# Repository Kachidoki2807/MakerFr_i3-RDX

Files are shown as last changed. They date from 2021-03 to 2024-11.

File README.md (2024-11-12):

# MakerFr i3-RDX <!-- omit in toc -->

Ce dépôt contient tout le nécessaire pour construire une MakerFr i3-RDX.
<p align="center">
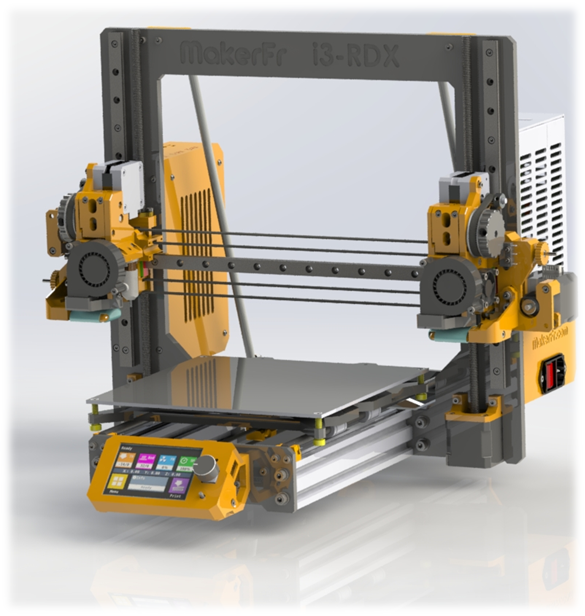
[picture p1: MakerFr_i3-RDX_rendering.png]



</p>

# Table des contenus <!-- omit in toc -->
- [Tutoriel de montage](#tutoriel-de-montage)
- [Cadre](#cadre)
- [Pièces à imprimer](#pièces-à-imprimer)
- [Pièces à sourcer](#pièces-à-sourcer)
- [Firmware BTT Octopus v1.1](#firmware-btt-skr-pro-12)
- [Firmware BTT TFT35](#firmware-btt-tft35)
- [PrusaSlicer - MakerFr Edition + .INI pour PrusaSlicer "normal"](#prusaslicer---makerfr-edition)

## Tutoriel de montage
[Disponible dans le dépôt](./PDF/)

## Cadre

[Disponible dans le dépôt](./Frame/)

## Pièces à imprimer

[Disponibles dans le dépôt](./STL/)

## Pièces à sourcer

[Disponibles dans le dépôt](./BOM/)

## Firmware BTT Octopus 1.1 (version 2.1.2.4 upgradé)

### Pourquoi cette version spéciale ? <!-- omit in toc -->
Dans la release 2.0.7.2 de MarlinFirmware, il y a un bug concernant la ventilation, empêchant l'utilisation correcte des modes de duplication (Duplication / Miroir). Ce bug a été corrigé par l'équipe de MakerFr et intégré dans MarlinFirmware, cependant il n'y a pas eu de nouvelle release depuis la correction. Afin de garantir la cohérence du code et de sa configuration (la branche bugfix est en constante évolution et n'est pas garantie fonctionnelle à tout instant), il est nécessaire de proposer une version spécifique MakerFr dans un état stable.

Il s'agit d'une branche basée sur le tag 2.0.7.2 dans laquelle ont été intégrés la configuration pour la MakerFr i3-RDX ainsi qu'un cherry pick (sorte de copier/coller) du correctif qui a été introduit dans la branche bugfix.

~~Ceci en attendant une éventuelle 2.0.7.3 qui intègrera nativement ce correctif.~~ Version 2.1.2.4 disponible

### Fichiers <!-- omit in toc -->
[Sources de MarlinFirmware modifié](https://github.com/Kachidoki2807/Marlin/tree/MakerFr_2.0.7.2_bugfix%2321206)

[Binaire pré-compilé pour Octopus 1.1 de BTT](/Firmware/BTT_Octopus/firmware.bin)

Le fichier .bin est à mettre sur la carte µSD de la BTT SKR PRO 1.2. Il sera automatiquement renommé en .CUR après la mise à jour.

## Firmware BTT TFT35
Concernant le TFT, le problème est tout autre. Il n'y a aucune gestion de version dans le dépôt officiel du constructeur. Ainsi le firmware évolue de jour en jour, sans aucune cohérence ni garantie d'un état stable. La maintenance devient alors très pénible.

~~Pour palier à cela, chez MakerFr on vous propose une "version" figée qui date de début 2021, avec laquelle nous avons travaillé depuis. La configuration est adaptée à l'i3-RDX.~~ MISE A JOUR FAITE EN 2024.

[Binaire pré-compilé pour le TFT35 de BTT](Firmware/BTT_TFT35/BIGTREE_TFT35_V3.0.26.x.bin)

Copier tout le contenu de ce dossier sur la carte SD du BTT TFT35. Les différents éléments seront automatiquement renommés en .CUR après la mise à jour.

> **Astuce :** N'oubliez pas qu'il vous est possible de télécharger le contenu de tout ce présent dépôt d'un seul bloc en [ZIP](../../archive/refs/heads/master.zip).

## PrusaSlicer - MakerFr Edition (Fichiers .ini pour PrusaSlicer "normal" dispo)

### Pourquoi cette édition ? <!-- omit in toc -->
Cette édition spéciale corrige certaines imperfections de PrusaSlicer concernant la gestion de la ventilation, ainsi que la dimension de la tour de purge.

Mais elle intègre également un tout nouveau profil constructeur, qui contient une série de paramètres prédéfinis. Ainsi il n'y a qu'à passer par le configurateur pour avoir un slicer en état de générer un G-Code compatible avec l'i3-RDX d'un clic.

Une réflexion est en cours sur la suite à donner à cette édition, des tickets supports on été ouvert chez Prusa, mais pas encore résolu. Concernant le profil constructeur, il pourra également évoluer indépendamment du slicer. Une intégration dans la base de profils de Prusa est envisageable, mais il faudra probablement l'étoffer un peu avant d'en arriver là.

### Fichiers <!-- omit in toc -->
Les sources seront peut-être mises à disposition dans l'avenir.

[Application pré-compilée pour Windows](../../raw/master/Slicer/PrusaSlicer%20-%20MakerFr%20Edition.zip)

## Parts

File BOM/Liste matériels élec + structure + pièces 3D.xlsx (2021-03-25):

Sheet: visserie
Tete / Type | Designation | Elec unit | EX1 | EX2 | Structure | Spool holder x 2 | Nb unités dénombré | arrondi sup | vis express | lot de | Tarif lot | Nb lot | PU ( pour info)
FHC | M3x8 | 0 | 0 | 0 | 2 | 0 | 2 | 5 | https://www.vis-express.fr/fr/vis-mx-fhc-inox-a4-din-7991/38157-936385-vis-metaux-fhc-tete-fraisee-empreinte-hexagonale-creuse-3x6-inox-a4-3663072419063.html | 10 | 0.23 | 1 | 0.02
FHC | M3x12 | 0 | 0 | 0 | 2 | 0 | 2 | 5
FHC | M3x25 | 0 | 0 | 0 | 4 | 0 | 4 | 10
CHC | M2x10 | 0 | 2 | 2 | 6 | 0 | 10 | 10
CHC | M3x6 | 0 | 3 | 1 | 18 | 0 | 22 | 30 | https://www.vis-express.fr/fr/vmx-chc-t-basse-a2-din-7984/40584-464799-vis-metaux-chc-btr-tete-bas-hc2-3x6-filetage-total-inox-a2-3663072196216.html | 10 | 3.6 | 1 | 0.12
CHC | M3x8 | 2 | 3 | 2 | 24 | 0 | 31 | 40 | https://www.vis-express.fr/fr/vmx-chc-t-basse-a2-din-7984/40585-970488-vis-metaux-chc-btr-tete-bas-hc2-3x8-filetage-total-inox-a2-3663072218895.html | 10 | 3.6 | 1 | 0.12
CHC | M3x10 | 0 | 0 | 0 | 12 | 0 | 12 | 30 | https://www.vis-express.fr/fr/vmx-chc-t-basse-a2-din-7984/40586-464815-vis-metaux-chc-btr-tete-bas-hc2-3x10-filetage-total-inox-a2-3663072196223.html | 10 | 0.23 | 3 | 0.02
CHC | M3x12 | 4 | 0 | 0 | 18 | 8 | 30 | 30
CHC | M3x16 | 2 | 4 | 4 | 38 | 2 | 50 | 50 | https://www.vis-express.fr/fr/vmx-chc-t-basse-a2-din-7984/40588-464831-vis-metaux-chc-btr-tete-bas-hc2-3x16-filetee-sur-12-inox-a2-3663072196230.html | 30 | 3.76 | 2 | 0.12
 |  |  |  |  |  | 0 | 0 |  |  | 10 | 2.76 | 1 | 0.28
CHC | M3x20 | 0 | 4 | 4 | 15 | 0 | 23 | 30 | https://www.vis-express.fr/fr/vmx-chc-t-basse-a2-din-7984/40589-464839-vis-metaux-chc-btr-tete-bas-hc2-3x20-filetee-sur-12-inox-a2-3663072223165.html | 10 | 0.24 | 1 | 0.02
CHC | M3x30 | 0 | 4 | 4 | 2 | 0 | 10 | 10 | https://www.vis-express.fr/fr/vmx-chc-t-basse-a2-din-7984/40591-464855-vis-metaux-chc-btr-tete-bas-hc2-3x30-filetee-sur-12-inox-a2-3663072378766.html | 10 | 0.54 | 2 | 0.05
CHC | M4x6 | 0 | 0 | 0 | 5 | 0 | 5 | 5
CHC | M4x8 | 0 | 0 | 0 | 0 | 0 | 0 | 5
CHC | M4x16 | 4 | 0 | 0 | 0 | 0 | 4 | 5
CHC | M5x16 | 0 | 0 | 0 | 16 | 0 | 16 | 20 | https://www.vis-express.fr/fr/vis-metaux-chc-btr-trou-de-guidage-acier/31608-980083-vis-metaux-chc-btr-5x16-classe-88-tete-basse-trou-acier-3663072368194.html | 20 | 3.18 | 2 | 0.32
H | M5x30 | 0 | 0 | 1 | 0 | 0 | 1 | 1
 | Ecrou M5 | 0 | 0 | 1 | 0 | 0 | 1 | 1
 | Ecrou M4 | 4 | 0 | 0 | 0 | 0 | 4 | 5
 | Ecrou M3 0.8d | 0 | 10 | 10 | 81 | 10 | 111 | 120
 | Ecrou M8 | 0 | 0 | 0 | 6 | 0 | 6 | 10
Plate étroite | Rondelle 3 |  |  |  |  |  | 32 | 50
Plate étroite | Rondelle 5 | 6 | 0 | 3 | 16 | 0 | 25 | 30
Plate étroite | Rondelle 8 | 0 | 0 | 0 | 4 | 0 | 4 | 5
 | ressort L12 mm D 5 interne | 0 | 0 | 1 | 0 | 0 | 1 | 1 | issu de la liste matos general, ressort d'UM2

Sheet: matos general
check | désignation | Source | Prix Unitaire | Nb | Ss total
Mécanique
o | Vslot noir 400 mm ( pour recoupe de 2 x ( 235mm + 105mm) ) | https://www.aliexpress.com/item/Black-100-500mm-2040-V-Slot-Aluminum-for-CNC-DIY-Laser-Engraving-3D-Printers-Camera-Slider/4001287484543.html | 7.34 € | 2 | 14.68 €
o | MGN12 H + rail 400mm | https://fr.aliexpress.com/item/32861278496.html?spm=a2g0s.9042311.0.0.27426c37sMZzYj | 13.95 € | 1 | 13.95 €
o | MGN12 H + rail 300mm | https://www.aliexpress.com/item/12mm-Linear-Guide-MGN12-L-100-200-300-350-400-450-500-550-600-700-800/32861278496.html | 12.12 € | 2 | 24.24 €
o | chariot MGN12H | https://fr.aliexpress.com/item/32861278496.html?spm=a2g0s.9042311.0.0.27426c37sMZzYj | 5.16 € | 1 | 5.16 €
o | Pignon GT2 16 dents alesage 5 mm | https://www.aliexpress.com/item/5PCS-16-teeth-GT2-Timing-Pulley-Bore-5mm-for-Rubber-2GT-Open-Timing-belt-width-6mm/33017482340.html | 2.83 € | 1 | 2.83 €
o | Poulie GT2 16 dents sur roulements - axe 3 mm | https://www.aliexpress.com/item/16T-20T-GT2-Aluminum-Timing-Pulley-With-Without-Tooth-For-DIY-3D-Printer/32885958954.html | 0.64 € | 3 | 1.92 €
o | Pignon GT2 60 dents axe 5 mm - lot de 3 | https://www.aliexpress.com/item/60-Teeth-GT2-Timing-Pulley-Bore-5-6-6-35-8-10-12-14-15mm-for/32993060755.html | 10.87 € | 1 | 10.87 €
o | Courroie ouverte 2GT par 5m, choisir "Type C" | https://www.aliexpress.com/item/5M-2GT-open-timing-Belt-6mm-PU-with-Steel-Core-Rubber-fiberglass-timing-belt-GT2-6mm/32859410237.html | 3.45 € | 1 | 3.45 €
o | Courroie fermée 2GT L=150 mm | https://www.aliexpress.com/item/GKTOOLS-C-3-3D-Printer-Parts-GT2-6mm-Closed-Loop-Rubber-Timing-Belt-2GT-Length-140/4000307058782.html | 0.34 € | 2 | 0.68 €
o | Lot 4 guidages linéaires à billes LM8UU | https://www.aliexpress.com/item/4PCS-LM8UU-Linear-Bearings-LM3UU-LM4UU-LM5UU-LM6UU-LM10UU-LM12UU-LM13UU-LM16UU-LM20UU-Linear-Bushing-8mm/32873055960.html | 3.00 € | 1 | 3.00 €
o | Tige lisse D=8 mm L=400 mm | https://www.aliexpress.com/item/6mm-8mm-10mm-12mm-16mm-linear-shaft-L-100-150-200-250-300-350-400-500/32560455225.html | 7.85 € | 2 | 15.70 €
o | Lot de 20 spacers 8 mm M3 | https://www.aliexpress.com/item/5-50pcs-Hex-Female-to-Female-M2-M2-5-M3-M4-M5-brass-standoff-spacer-Hexagonal/4000239735518.html | 0.94 € | 1 | 0.94 €
o | Kit bondtech gears | https://www.aliexpress.com/item/Drivegear-kit-dual-drive-gear-extruder-kit-Cloned-Btech-upgrade-for-extruder-for-Prusa-i3-3d/32959764680.html | 6.74 € | 2 | 13.48 €
o | Feuille auto collante bed | https://www.aliexpress.com/item/3D-printer-Parts-1-pcs-Frosted-Heated-bed-Sticker-printing-Build-Sheets-build-plate-tape-Platform/32842476025.html | 3.27 € | 2 | 6.54 €
 | 2 Pads silicone prédécoupés |  | 0.00 € | 1 | 0.00 €
 | Cadre spécifique i3 RDX - valchromat |  | 0.00 € | 1 | 0.00 €
 | Kit de pieces imprimées i3 RDX |  | 0.00 € | 1 | 0.00 €
o | kit 5 ressort UM2 | https://fr.aliexpress.com/item/32604418352.html?scm_id=1007.14976.191224.0&scm-url=1007.14976.191224.0 | 0.71 € | 1 | 0.71 €
 | Tige lisse 5mm longueur 51mm | Casto, Leroy merlin |  | 1 | 0.00 €
 | Tige fileté de diamètre 8mm L = 360mm | Casto, Leroy merlin |  | 1 | 0.00 €
 | 4 Roulement MR105RS | https://fr.aliexpress.com/item/32949998854.html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 | 6.94 | 1 | 6.94 €
o | Lot de 4 vis ajustement bed + ressort 15x6x3, couleur au choix | https://fr.aliexpress.com/item/4000143856235.html | 2.73 | 1 | 2.73 €
 |  |  |  | Sous-total | 127.82 €
Electricité
 | Machine bien bruyante !!!!! ;-) |  |  |  |  |  | Option SILENCE = "fan 40 mm sliencieux" pour hotends
 |  |  |  |  |  |  |  |  | Prix unitaire | Nb | Ss total
o | Heat bed aimanté + feuille acier | https://www.aliexpress.com/item/220-220mm-3D-Printer-MK3-Magnetic-Heated-Bed-24V-Wiring-Thermistor-Kit-With-Steel-Sheet-For/32960562213.html | 35.20 € | 1 | 35.20 €
o | Alim 24 V 400 W | https://www.aliexpress.com/item/Switch-Power-Supply-for-Led-strip-Adapter-AC-110-220V-to-DC-24V-20A-480W-Transformer/32771311343.html | 19.17 € | 1 | 19.17 € |  | Fan 4010 de prusa mk3, lot de 2 (sur Store Fysetc sur le web) | https://www.fysetc.com/products/fysetc-prusa-i3-mk3-cool-blower-fan-4010-40x40x10mm-dc-5v-0-2a-hotend-cooler-radiator-for-3d-printer-diy-parts-accessories-2pc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 | 12.99 | 1 | 12.99
o | BTT SKR Pro 1.2 + 6 TMC2209 | https://fr.aliexpress.com/item/33037993926.html?spm=a2g0w.12010612.8148356.31.29f41e73Z66uXW | 63.74 € | 1 | 63.74 € |  | OU
o | BL Touch Original + rallonge fils | https://fr.aliexpress.com/item/33025648093.html?spm=a2g0w.12010612.8148356.1.6fb7d78azxapbg | 29.83 € | 1 | 29.83 € |  | régulateur DC/DC 24V / ajustable | https://www.amazon.fr/VABNEER-LM2596S-Alimentation-convertisseur-Converter/dp/B072MQYJ93/ | 3.33 € | 1 | 3.33 €
o | E3D v6 clone kit (hotend,etc dont fan 30 mm) - 24 V- 1.75 mm All metal | https://fr.aliexpress.com/item/32844028127.html | 13.79 € | 2 | 27.58 € | si pas fan 30mm | Fan noctua 5V | https://www.amazon.fr/Noctua-NF-A4x10-FLX-Ventilateur-40x40x10mm/dp/B00NEMGCIA?th=1 | 12.90 € | 2 | 25.80 €
o | Ecran TFT35 V3.0 Bigtreetech | https://fr.aliexpress.com/item/4000051197496.html | 23.35 € | 1 | 23.35 €
o | Blower 5015 | https://www.aliexpress.com/item/Aokin-DC-12V-24V-50mm-Blow-Radial-Cooling-Fan-Hotend-Extruder-For-RepRap-3D-Printer-Accessories/32972702280.html | 1.49 € | 2 | 2.98 € | OU | 2 Blower 5 V FYSETC prusa i3 Mk3 | https://fr.aliexpress.com/item/32961572014.html | 5.4 | 1 | 5.4
o | Lot 10 mico switches sans levier | https://www.aliexpress.com/item/10-PCS-LOT-Limit-Switch-3-Pin-2-Pin-High-quality-and-long-life-All-New/32273125391.html | 1.36 € | 1 | 1.36 € |  | (ou sur Store Fysetc sur le web) | https://www.fysetc.com/products/prusa-i3-mk3-3d-printer-parts-dc-5v-5015-50mm-blow-radial-cooling-fan-hydraulic-sleeve-bearing-front-print-fan-cooler-radiator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 | 2.9 | 2 | 5.8
o | Gaine tressée 4 mm | https://www.aliexpress.com/item/5-10M-Black-Insulated-Braid-Sleeving-2-4-6-8-10-12-15-20-25mm-Tight/4000111680202.html | 2.11 € | 1 | 2.11 €
o | Gaine tressée 10 mm | https://www.aliexpress.com/item/5-10M-Black-Insulated-Braid-Sleeving-2-4-6-8-10-12-15-20-25mm-Tight/4000111680202.html | 3.37 € | 1 | 3.37 €
o | Fils N+R 16AWG 1m + 1m | https://www.aliexpress.com/item/1meter-Black-1meter-Red-Silicon-Wire-12AWG-14AWG-16AWG-22AWG-24AWG-Heatproof-Soft-Silicone-Silica-Gel/32807592656.html | 3.11 € | 2 | 6.22 €
o | Cable N+R 18AWG 5m | https://fr.aliexpress.com/item/32867632555.html | 4.19 € | 1 | 4.19 € |  | ceci est une variante de contitution stepper Z en 3 pîeces.
o | Lot 3 steppers nema 17 42 | https://www.aliexpress.com/item/Rtelligent-Nema-17-Stepper-Motor-38mm-42motor-Nema17-42BYGH-42N-cm-59-5oz-in-4-lead/4000329570564.html | 20.32 € | 1 | 20.32 € | OU | lot de 5 steppers nema 17 42 | https://fr.aliexpress.com/item/4001233582423.html | 29.99 | 1 | 29.99
o | Stepper nema 17 42 avec vis trap 400 mm 8x2 + nut | https://fr.aliexpress.com/item/4000317880757.html?spm=a2g0s.9042311.0.0.27426c37CUPDoi | 14.56 € | 2 | 29.12 € | OU | lot de 5 coupleurs 5-8 | https://fr.aliexpress.com/item/4000200182255.html | 2.76 | 1 | 2.76
 |  |  |  |  |  |  | vis trap 400 mm 8x2 + nut | https://fr.aliexpress.com/item/32970585911.html | 5.13 | 2 | 5.13
o | Prise IEC320 | https://www.aliexpress.com/item/1PC-IEC320-C14-AC-Power-Cord-Inlet-Socket-Receptacle-With-Rocker-Switch-250V-15A-SA172-P50/32745809311.html | 0.88 € | 1 | 0.88 € |  |  |  |  |  | 37.88
o | Lot 2 fan 6010 24 V XH 2.54 | https://www.aliexpress.com/item/2-Pcs-Gdstime-60mm-5V-12V-24V-Brushless-USB-2PIN-3PIN-DC-Cooler-Fan-60x60x10mm-6010/32571979071.html | 7.42 € | 1 | 7.42 €
o | Lot de 3 Stepper nema 17 28mm 12Ncm | https://fr.aliexpress.com/item/4000123671533.html | 14.71 € | 1 | 14.71 €
 | Ruban Led NeoPixel 30 cm |  | 0.00 € | 1 | 0.00 €
o | Connecteur JST 2.54 mm pré cablé 2 fils - 2pins - 30 cm set10 | https://fr.aliexpress.com/item/32996835431.html | 1.18 € | 1 | 1.18 € |  |  |  |  | Option 2
o | Connecteur JST 2.54 m pré cablé 3 fils - 3pins - 30 cm set10 | https://fr.aliexpress.com/item/32996835431.html | 1.34 € | 1 | 1.34 € |  |  |  |  | total | 425.90 €
o | Set de gaine thermorétracable | https://fr.aliexpress.com/item/4000350274023.html | 7.83 € | 1 | 7.83 €
o | Attache cables (Colring 2.5 mm x 100) | https://fr.aliexpress.com/item/32879228786.html | 1.37 € | 1 | 1.37 €
o | kit de 2 nappes 60 cm pour LCD | https://fr.aliexpress.com/item/4000066479183.html?spm=a2g0s.9042311.0.0.27426c37Ac1qRe | 2.95 € | 1 | 2.95 €
o | Prolongateur TFT (JST-XH 4s 20cm), choisir 4S | https://fr.aliexpress.com/item/32238535012.html?scm_id=1007.16891.96945.0&scm-url=1007.16891.96945.0 | 3.42 € | 1 | 3.42 €
 |  |  |  | Sous-total | 309.64 €
 |  |  |  |  |  |  |  |  |  | Option 2- silence
 |  |  |  | Option 1 |  |  |  |  |  | total | 471.99 €
 |  |  |  | total | 437.46 €

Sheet: Pièces imprimées
Désignation | Nb | Matériau | Infill | étape tuto | present dans dossier step+ stl | étape tuto
Anti oozing
Porte lame anti oozing | 2 | PLA | 25 | 58 | x | 58
Support anti oozing X0 | 1 | PLA | 25 | 60 | x | 60
Support anti oozing X1 | 1 | PLA | 25 | 61 | x | 61
Axe X - Z
Liaison Z-T8 | 1 | PLA | 50 | 25 | x | 25
Liaison Z-T8- mirror | 1 | PLA | 50 | 25 | x | 25
X motor base | 2 | PETG | 80 | 23 | x | 23
Ajusteur X1 vs X0 | 1 | PLA | 50 | 53 | x | 53
Chariot X0 | 1 | PLA | 25 | 33 | x | 33
Chariot X1 | 1 | PLA | 25 | 33 | x | 33
Support Z motor | 2 | PETG | 50 | 26 | x | 26
X belt holder-X0 only | 1 | PLA | 50 | 36 | x | 36
X belt holder-X1 only | 1 | PLA | 50 | 36 | x | 36
X-motor-Arc X0 | 1 | PETG | 50 | 30 | x | 30
X-motor-Arc X1 | 1 | PETG | 50 | 30 | x | 30
Slider-belt-tension | 2 | PETG | 50 | 32 | x | 32
Scroll Wheel | 2 | PLA | 50 | 33 | x | 33
Electro
Cover_SKR_Box | 1 | PLA | 50 | 82 | x | 82
Pince cable BOX | 1 | PLA | 25 | 81 | x | 81
PSU enclosure_113x49 | 1 | PLA | 50 | 20 | x | 20
PSU enclosure_115x50 | 1 | PLA | 50 | 20 | x | 20
Quiet blower PSU-bicolore | 1 | PLA | 25 | 20 | x | 20
Quiet blower PSU-bicolore-insert | 1 | PLA | 25 | 20 | x | 20
SKR Box | 1 | PLA | 50 | 22 | x | 22
cover conn heatbed | 1 | PLA | 50 |  | x
Appui PSU sur tige 8 | 1 | PLA | 25 | 21 | x | 21
Spool holders
Spool holder - arm | 2 | PLA | 25 | 65 | x | 65
Spool holder - arm - mirror | 2 | PLA | 25 | 65 | x | 65
Rond spool holder - partie 1 | 2 | PLA | 25 | 64 | x | 64
Rond spool holder - partie 2 | 2 | PLA | 25 | 64 | x | 64
Spool holder - stab | 2 | PLA | 25 | 65 | x | 65
Structure
Back corner | 1 | PETG | 25 | 6 | x | 6
Back corner - mirror | 1 | PETG | 25 | 6 | x | 6
TFT cover | 1 | PLA | 100 | 62 | x | 62
TFT holder | 1 | PLA | 50 | 17 | x | 17
TFT holder - mirror | 1 | PLA | 50 | 17 | x | 17
Y-Renforcement-front | 1 | PLA | 25 | 4 | x | 4
Y-Renforcement-front-mirror | 1 | PLA | 25 | 4 | x | 4
Y-Renforcement-back | 1 | PLA | 25 | 4 | x | 4
Z-Renforcement | 1 | PETG | 25 | 5 | x | 5
Z-Renforcement- mirror | 1 | PETG | 25 | 5 | x | 5
Axe Y
Arm - Y belt tensioner | 1 | PLA | 50 | 12 | x | 12
Base - Y belt tensioner | 1 | PLA | 50 | 12 | x | 12
Y-belt | 1 | PLA | 50 | 14 | x | 14
Y_holder front | 2 | PLA | 50 | 8 | x | 8
Y_holder back | 2 | PLA | 50 | 9 | x | 9
Y-motor | 1 | PLA | 50 | 11 | x | 11
Pieces communes extrudeurs
Extrud-idler-X0_X1 | 2 | PLA | 25 | 43 | x | 43
Bltouch_holder-X0 | 1 | PLA | 25 | 46 | x | 46
Fan_duct-X0_X1 | 2 | PLA | 50 | 49 | x | 49
Bague extrudeur | 2 | PLA | 50 | 42 | x | 42
Extrudeurs T0 & T1 (X1 & X2) - version fan 3010 (livrés avec hotends)
Extrud_A- X0-for 3010 | 1 | PLA | 25 | 40 | x | 40
Extrud_B- X0-for 3010 | 1 | PLA | 25 | 40 | x | 40
Extrud_A- X1-for 3010 | 1 | PLA | 25 | 40 | x | 40
Extrud_B- X1-for 3010 | 1 | PLA | 25 | 40 | x | 40
Patte suppot blower X0 | 1 | PLA | 50 |  | x | 49
Space fan -X1 for 3010 | 1 | PLA | 50 |  | x | 52
Extrudeurs T0 & T1 (X1 & X2) - version fan 4010 (Noctua ou FYSETC )
Extrud_A- X0-for 4010-clip version | 1 | PLA | 25 | 40 | x | 40
Extrud_B- X0-for 4010-clip version | 1 | PLA | 25 | 40 | x | 40
Extrud_A- X1-for 4010-clip version | 1 | PLA | 25 | 40 | x | 40
Extrud_B- X1-for 4010-clip version | 1 | PLA | 25 | 40 | x | 40
patte suppot blower X2 3010 | 1 | PLA | 50 |  | x
Nb total de pieces | 36

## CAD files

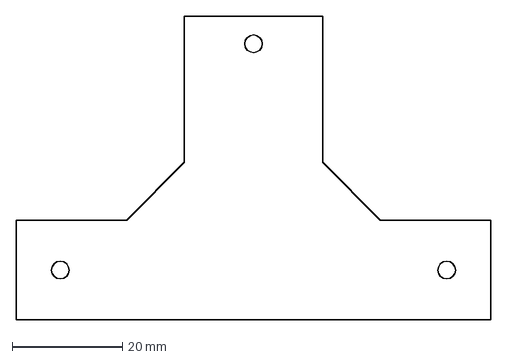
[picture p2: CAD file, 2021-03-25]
Antioozing_silicone_pad.DXF
86.0 x 55.0 mm

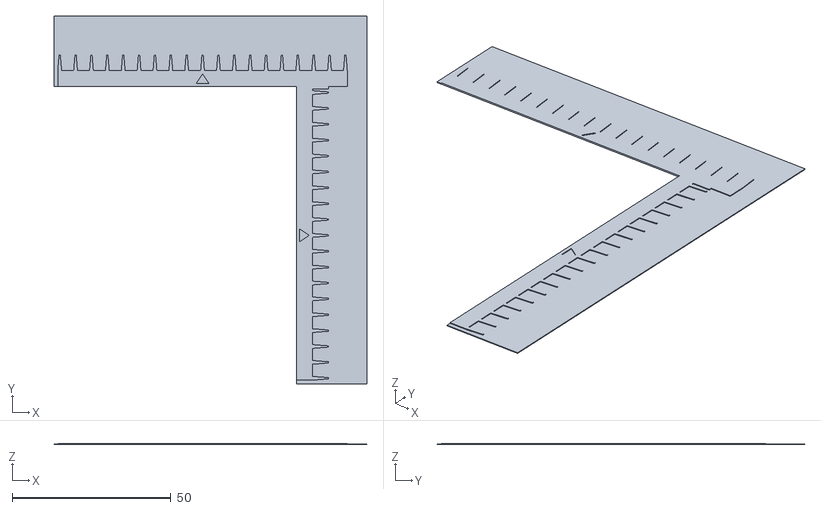
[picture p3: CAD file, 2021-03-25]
Calibration_parts/Vernier/vernier - calib1-1-1.STL
98.6 x 115.9 x 0.4

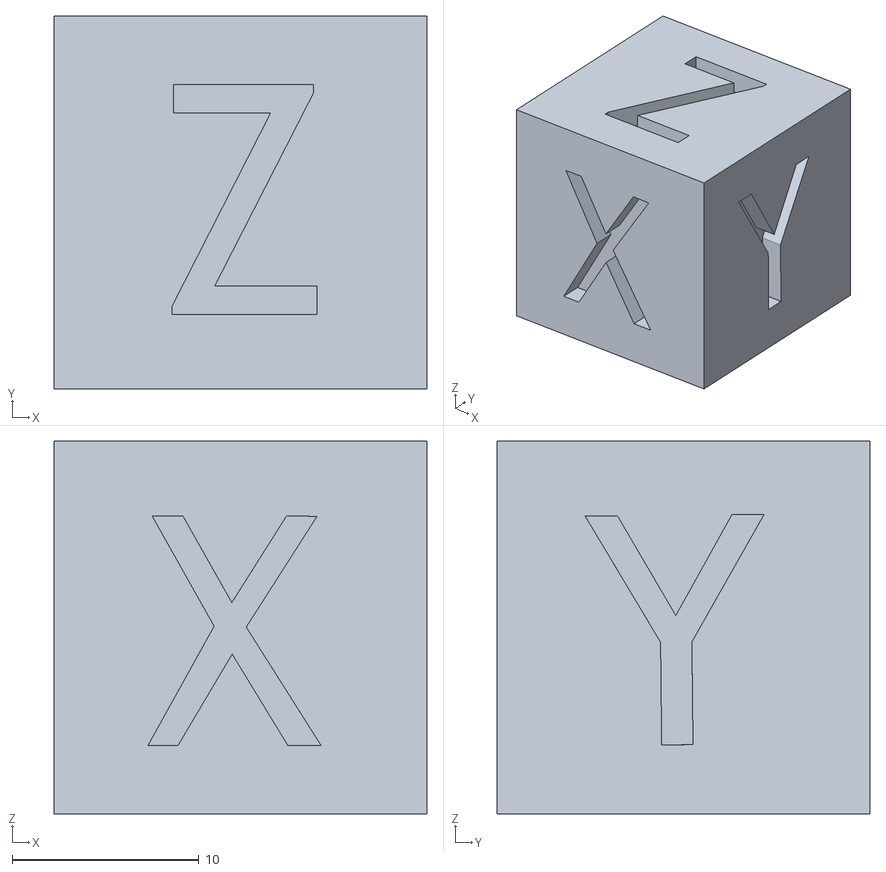
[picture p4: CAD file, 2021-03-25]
Calibration_parts/xyzCalibration_cube.stl
20.0 x 20.0 x 20.0

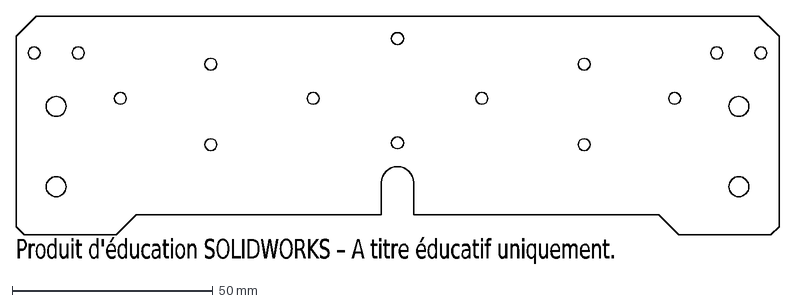
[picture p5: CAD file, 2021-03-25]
Frame/DXF/Frame_front-i3-RDX.DXF
Produit d'éducation SOLIDWORKS – A titre éducatif uniquement.

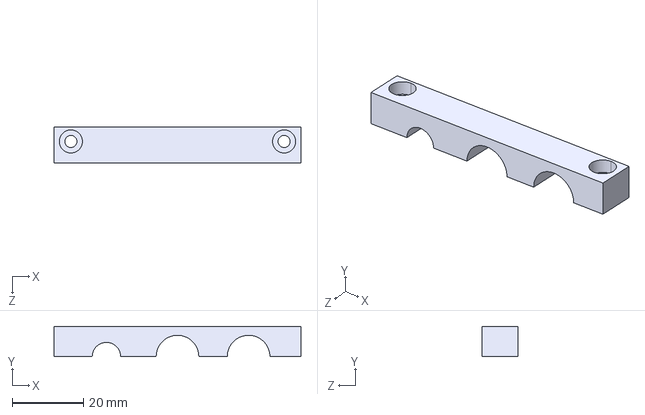
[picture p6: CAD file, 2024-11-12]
STEP/Box_BTT_Octopus/Clamp.STEP
69.5 x 8.50 x 10.0 mm

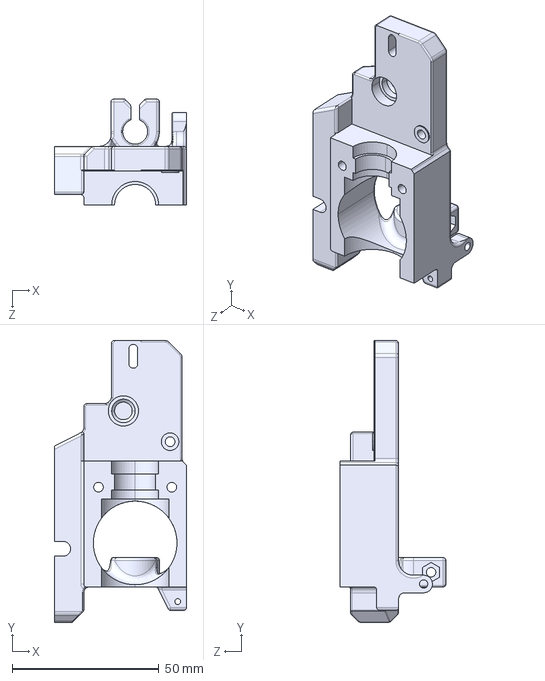
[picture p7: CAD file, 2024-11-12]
STEP/Extruders/EX1/A_2.STEP
45.0 x 96.1 x 36.1 mm

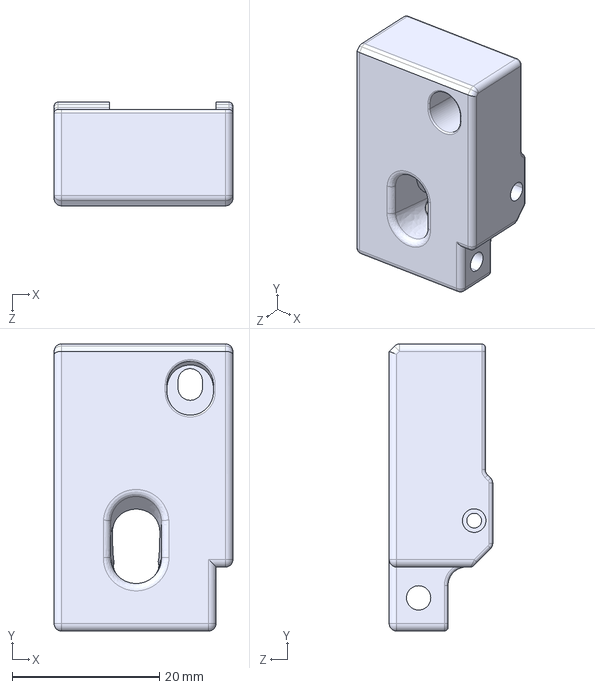
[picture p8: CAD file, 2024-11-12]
STEP/Extruders/EX2/B_Idler.STEP
24.3 x 39.0 x 14.1 mm

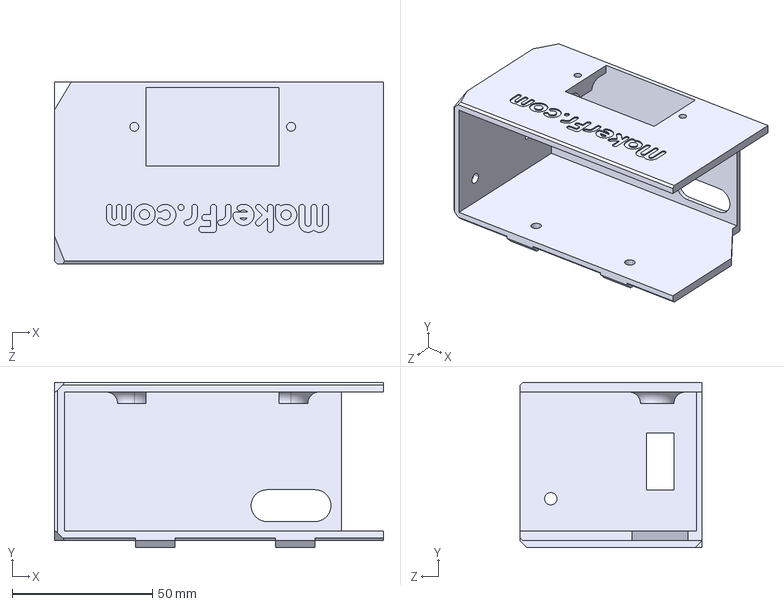
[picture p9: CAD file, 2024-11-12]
STEP/Other/PSU.STEP
117.5 x 59.1 x 65.0 mm

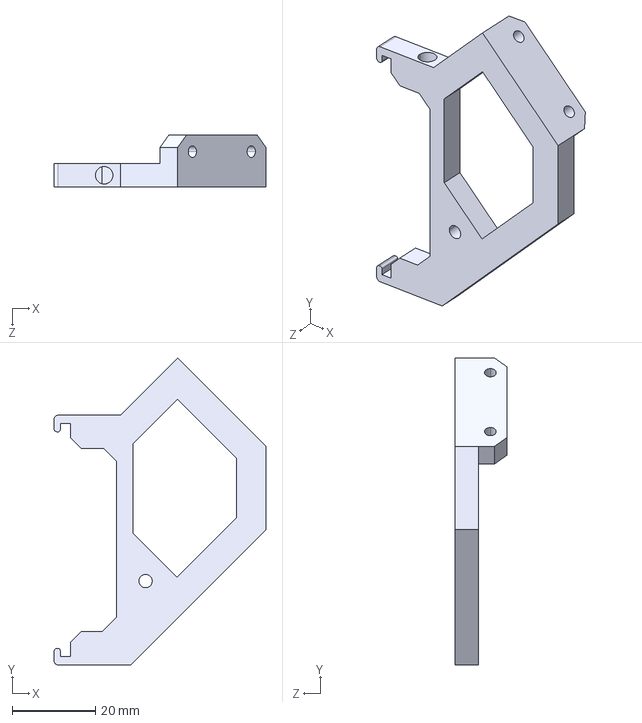
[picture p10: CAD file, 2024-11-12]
STEP/Screen/Right_arm.STEP
50.9 x 73.7 x 12.5 mm

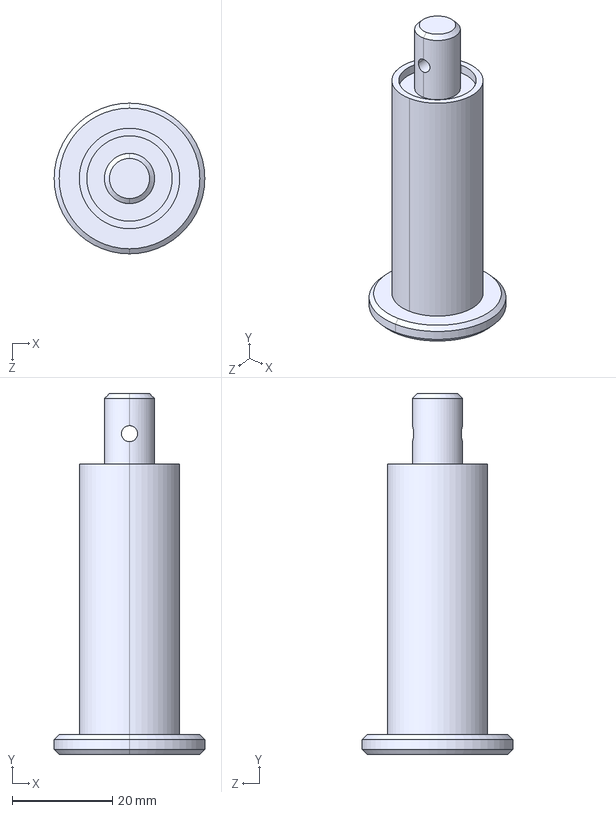
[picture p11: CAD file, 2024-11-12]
STEP/Spool_Holder/Part2.STEP
30.0 x 71.9 x 30.0 mm

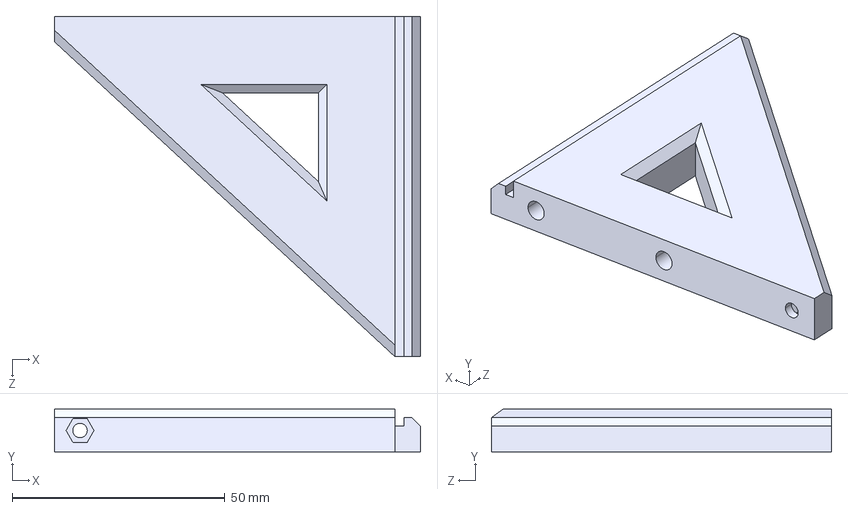
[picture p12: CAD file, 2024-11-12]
STEP/Y_axis/Y_renforcement_back.STEP
86.0 x 10.0 x 80.0 mm

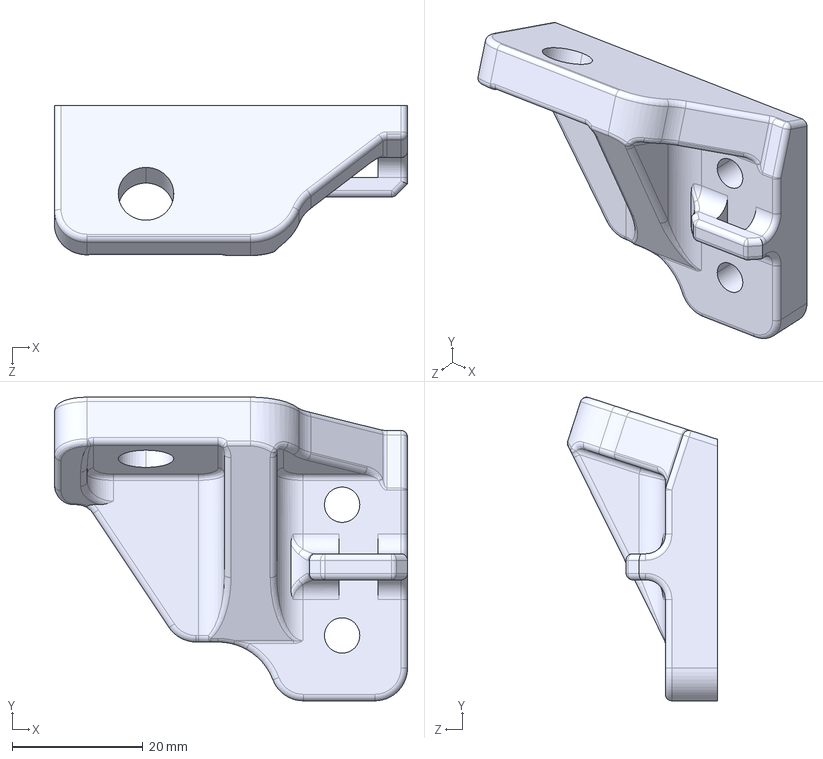
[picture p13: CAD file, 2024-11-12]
STEP/Z_axis/Left_renforcement.STEP
54.0 x 46.5 x 23.0 mm

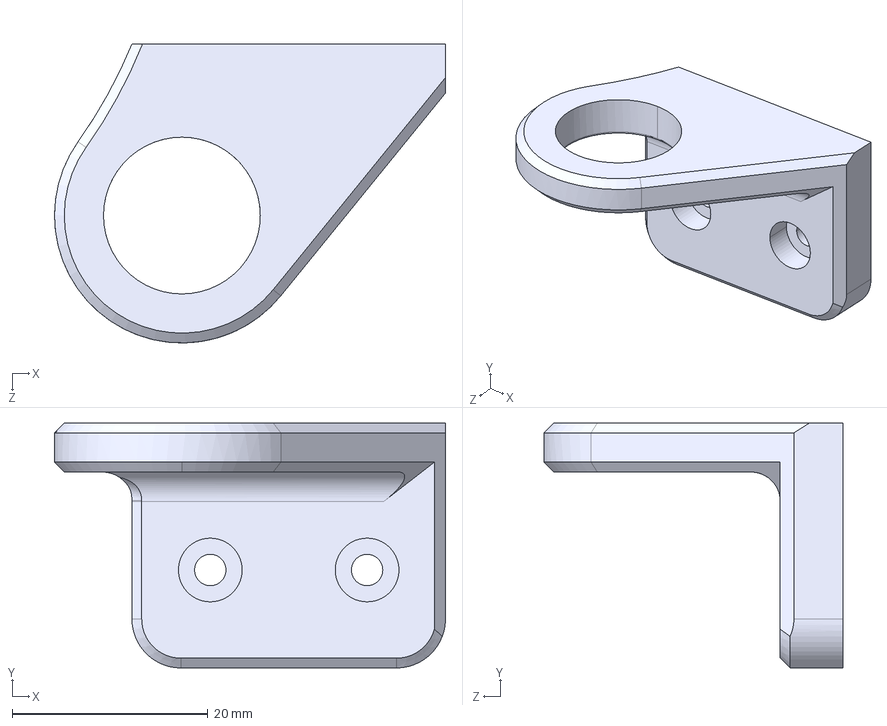
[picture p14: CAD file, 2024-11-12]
STEP/Z_Belt/Right.STEP
39.9 x 25.0 x 30.5 mm

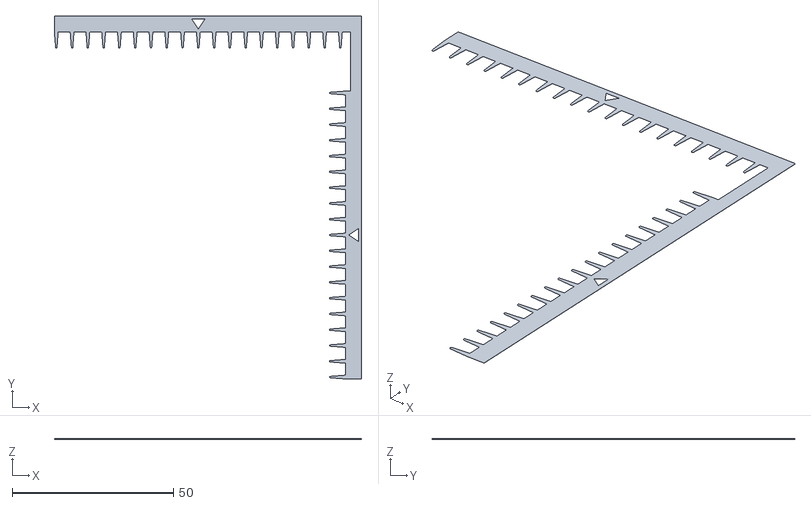
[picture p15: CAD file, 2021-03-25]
Calibration_parts/Vernier/vernier - calib2-1-1.STL
95.4 x 112.7 x 0.2

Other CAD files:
Frame/DXF/Frame_back-i3-RDX.DXF
STEP/Box_BTT_Octopus/Cover.STEP
STEP/Extruders/EX1/A_1.STEP
STEP/Extruders/EX2/B_2.STEP
Frame/DXF/Cadre i3-RDX.DXF
Frame/DXF/Frame_plate-i3-RDX.DXF
STEP/Box_BTT_Octopus/Box.STEP
STEP/Extruders/EX1/A_Carriage.STEP
STEP/Extruders/EX1/A_Fan_duct.STEP
STEP/Extruders/EX1/A_Idler.STEP
STEP/Extruders/EX1/E_motor_holder.STEP
STEP/Extruders/EX1/Spacer.STEP
STEP/Extruders/EX2/B_1.STEP
STEP/Extruders/EX2/B_Carriage.STEP
STEP/Extruders/EX2/B_Fan_duct.STEP
STEP/Extruders/EX2/B_Z_offset.STEP
STEP/Extruders/EX2/E_motor_holder.STEP
STEP/Extruders/EX2/Spacer.STEP
STEP/Other/Dumper_2020_profile.STEP
STEP/Screen/Left_arm.STEP
STEP/Screen/TFT35_BOX.STEP
STEP/Spool_Holder/1.STEP
STEP/Spool_Holder/2.STEP
STEP/Spool_Holder/3.STEP
STEP/Spool_Holder/4.STEP
STEP/Spool_Holder/Part1.STEP
STEP/Spool_Holder/Stab.STEP
STEP/Y_axis/Belt_holder.STEP
STEP/Y_axis/Idler_arm.STEP
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

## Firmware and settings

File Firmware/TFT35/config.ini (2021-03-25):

#--------------------------------------------------------------------
#
# DEFAULT CONFIG FILE FOR BigTreeTech TFT CONTROLLERS
#
#--------------------------------------------------------------------


#--------------------------------------------------------------------
# Supported TFT Variants
#--------------------------------------------------------------------
#
# BIGTREE_TFT35_V1_0    / BIGTREE_TFT35_V1_1 / BIGTREE_TFT35_V1_2
# BIGTREE_TFT35_V2_0    / BIGTREE_TFT35_V3_0 / BIGTREE_TFT35_E3_V3_0
# BIGTREE_TFT35_B1_V3_0 / BIGTREE_TFT43_V3_0 / BIGTREE_TFT50_V3_0
# BIGTREE_TFT70_V3_0    / BIGTREE_TFT28_V1_0 / BIGTREE_TFT28_V3_0
# BIGTREE_TFT24_V1_1    / MKS_32_V1_4        / MKS_28_V1_0
#
# Firmware source: https://github.com/bigtreetech/BIGTREETECH-TouchScreenFirmware


#--------------------------------------------------------------------
# Supported Marlin Firmware Versions
#--------------------------------------------------------------------
#
# Minimum Marlin firmware version: 2.0.5.4
# Distribution date: 2020-05-12
# Firmware source: https://github.com/MarlinFirmware/Marlin/releases
#
# In order the TFT firmware is able to provide all of its functionalities/features,
# ensure that the following options are enabled in Marlin firmware.
#
# General options:
#   M115_GEOMETRY_REPORT (in Configuration_adv.h)
#   M114_DETAIL (in Configuration_adv.h)
#   REPORT_FAN_CHANGE (in Configuration_adv.h)
#   EMERGENCY_PARSER (in Configuration_adv.h)
#   SERIAL_FLOAT_PRECISION 4 (in Configuration_adv.h)
#   HOST_ACTION_COMMANDS (in Configuration_adv.h)
#
# Options to support printing from onboard SD:
#   SDSUPPORT (in Configuration.h)
#   AUTO_REPORT_TEMPERATURES (in Configuration_adv.h)
#   AUTO_REPORT_SD_STATUS (in Configuration_adv.h)
#   LONG_FILENAME_HOST_SUPPORT (in Configuration_adv.h)
#   SDCARD_CONNECTION ONBOARD (in Configuration_adv.h)
#
# Options to support (Un)Load menu:
#   FILAMENT_LOAD_UNLOAD_GCODES (in Configuration_adv.h)


#--------------------------------------------------------------------
# General Settings
#--------------------------------------------------------------------

#### Enable Status Screen
# Status screen or home screen displays the current temperature, fan and speeds.
# If this disabled, the main menu will become the default home screen.
#   Options: [Enable: 1, Disable: 0]
status_screen:1

#### Baudrate / Connection speed
# This baudrate setting is used for serial connection to the printer and other serial hosts like ESP8266.
#   Options: [2400: 0, 9600: 1, 19200: 2, 38400: 3, 57600: 4, 115200: 5, 250000: 6, 500000: 7, 1000000: 8]
baudrate:5

#### Default Touch Mode Language
# Select the language to display on the LCD while in Touch Mode.
# To add/flash a second language copy the required "language_xx.ini" file from "Language Packs" folder
# to the SD root folder. Then preset the reset button to load/flash the copied language file.
#   Options: [primary language (english): 0, secondary language: 1]
language:0

#### Default Touch Mode Colors
# Set colors used in touchscreen mode.
# Select an option from the provide list or set the color (RGB888 format) hex value directly (start with “0x”),
# such as: Red: 0xFF0000, Green: 0x00FF00, Blue: 0x0000FF.
#   Options: [ WHITE: 0,  BLACK: 1,  RED: 2,  GREEN: 3,      BLUE: 4,       CYAN: 5,  MAGENTA: 6,    YELLOW: 7,
#             ORANGE: 8, PURPLE: 9, LIME: 10, BROWN: 11, DARKBLUE: 12, DARKGREEN: 13,    GRAY: 14, DARKGRAY: 15]

## Title background color
title_back_color:1

## Background color
background_color:1

## Font foreground color
font_color:0

## Reminder font color, such as: "No print attached", "Busy processing", etc
reminder_color:2

## Volume status/reminder font color, such as: "Card inserted", "Card removed"
volume_status_color:5

## Backgroud color for X Y Z position display in Status Screen menu
status_xyz_bg_color:15

## List View border color
list_border_color:15

## List View button background color
list_button_bg_color:15

## Color used by the Mesh Editor menu for drawing the mesh with the minimun value in the grid
mesh_min_color:7

## Color used by the Mesh Editor menu for drawing the mesh with the maximum value in the grid
mesh_max_color:2

#### Rotate UI
# Rotate UI by 180 degrees.
#   Options: [enable: 1, disable: 0]
rotate_ui:0

#### Temperature ACK
# Show or hide temperature ACK in Terminal menu.
#   Options: [show: 1, hide: 0]
terminal_ack:0

#### Inverted Axes For Move Menu
# Invert axis button function in Move menu in order it matches the actual axis movement.
#   Format: [X<option> Y<option> Z<option>]
#   Options: [enable: 1, disable: 0]
invert_axis:X0 Y1 Z0

#### Persistent Temperature Info
# Show persistent temperature info on all menus.
#   Options: [enable: 1, disable: 0]
persistent_info:0

#### File List Mode
# Display files in list mode instead of icon mode.
#   Options: [enable: 1, disable: 0]
files_list_mode:1
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

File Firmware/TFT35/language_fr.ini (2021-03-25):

#### Language Code:FR
## Language Version:20210121
## Maximum byte per keyword is 250 Bytes.
## Escape characters are not supported except newline '\n'

label_language:Français
label_heat:Chauffer
label_move:Déplacer
label_home:Home
label_disable_steppers:Moteurs
label_print:Imprimer
label_extrude:Extruder
label_fan:Ventiler
label_settings:Options
label_screen_settings:Écran
label_machine_settings:Machine
label_feature_settings:Paramètres
label_sound:Son
label_touch_sound:Son des touches
label_toast_sound:Notifications
label_alert_sound:Popups et alertes
label_shut_down:Eteindre
label_rgb_settings:LED
label_rgb_off:LED Off
label_terminal:Terminal
label_custom:Gcode
label_leveling:Niveaux
label_point_1:Point 1
label_point_2:Point 2
label_point_3:Point 3
label_point_4:Point 4
label_point_5:Point 5
label_bed_leveling:ABL
label_bl_complete:Nivellement terminé
label_bl_smart_fill:Les points de sonde manquants\nont été intelligemment remplis.\n \nNote : n'oubliez pas de sauvegarder !
label_bl_enable:BL On
label_bl_disable:BL Off
label_abl:ABL
label_bbl:BBL
label_ubl:UBL
label_mbl:MBL
label_mbl_settings:Nivellement Mesh
label_abl_settings:Nivellement Automatique
label_abl_settings_bbl:Nivellement bilinéaire
label_abl_settings_ubl:Nivellement unifié
label_abl_settings_ubl_save:Enregistrer dans l'emplacement
label_abl_settings_ubl_load:Charger depuis l'emplacement
label_abl_slot0:Slot 0
label_abl_slot1:Slot 1
label_abl_slot2:Slot 2
label_abl_slot3:Slot 3
label_abl_slot_eeprom:Se souvenir de l'emplacement\nau prochain redémarrage ?\n(Sauvegarde EEPROM)
label_abl_z:Z Fade
label_bltouch:BLTouch
label_test:Tester
label_deploy:Déployer
label_stow:Rentrer
label_repeat:Répéter
label_z_offset:Z Offset
label_probe_offset:Décalage Palpeur
label_home_offset:Décalage Home
label_confirmation:Êtes-vous sûr ?
label_down:Descendre
label_up:Monter
label_save:Sauver
label_restore:Restaurer
label_reset:Reset
label_default:Défaut
label_clear:Effacer
label_next:Suivant
label_distance:Distance
label_invalid_value:Aucune valeur valide fournie !
label_timeout_reached:Délai d'attente dépassé !
label_process_running:Processus en cours ! Veuillez patienter
label_process_completed:Processus terminé !
label_process_aborted:Processus annulé !
label_inc:Plus
label_dec:Moins
label_nozzle:Buse
label_bed:Plateau
label_chamber:Caisson
label_start:Démarrer
label_stop:Stopper
label_back:Retour
label_page_up:Précédent
label_page_down:Suivant
label_pause:Pause
label_resume:Reprendre
label_load:Charger
label_unload:Décharger
label_load_unload:Charger/Décharger
label_load_unload_short:Dé/Charger
label_slow_speed:Lent
label_normal_speed:Normal
label_fast_speed:Rapide
label_fan_full_speed:Max
label_fan_half_speed:Moitié
label_rotate_ui:Rotation
label_touchscreen_adjust:Ajuster
label_more:Plus
label_screen_info:Infos
label_status:Statut
label_simulator_bg_color:Couleur de l'arrière-plan Marlin
label_simulator_font_color:Couleur de la police Marlin
label_white:Blanc
label_black:Noir
label_blue:Bleu
label_red:Rouge
label_green:Vert
label_cyan:Cyan
label_yellow:Jaune
label_brown:Marron
label_gray:Gris
label_orange:Orange
label_indigo:Indigo
label_violet:Violette
label_magenta:Magenta
label_purple:Violet
label_lime:Lime
label_darkblue:Bleu Foncé
label_darkgreen:Vert Foncé
label_darkgray:Gris Foncé
label_disconnect:Libérer
label_baudrate:Vitesse
label_percentage:Avancement
label_babystep:BabyStep
label_percentage_speed:Vitesse
label_percentage_flow:Débit
label_value_zero:Zéro
label_1_degree:1℃
label_5_degree:5℃
label_10_degree:10℃
label_x_inc:X+
label_y_inc:Y+
label_z_inc:Z+
label_x_dec:X-
label_y_dec:Y-
label_z_dec:Z-
label_x:X
label_y:Y
label_z:Z
label_001_mm:0.01mm
label_01_mm:0.1mm
label_1_mm:1mm
label_5_mm:5mm
label_10_mm:10mm
label_100_mm:100mm
label_200_mm:200mm
label_1_percent:1%
label_5_percent:5%
label_10_percent:10%
label_percent_value:%d%%
label_ready:Prête
label_busy:Occupée, veuillez patienter...
label_unconnected:Aucune imprimante connectée !
label_disconnect_info:Vous pouvez maintenant contrôler l'imprimante depuis votre ordinateur !
label_loading:Chargement...
label_power_failed:Continuer l'impression ?
label_continue:Continuer
label_cancel:Annuler
label_adjust_title:Calibration écran tactile
label_adjust_info:Veuillez toucher le point rouge
label_adjust_ok:Succès de l'ajustement
label_adjust_failed:Ajustement incorrect, veuillez réessayer
label_warning:Attention
label_stop_print:Arrêter l'impression ?
label_confirm:Confirmer
label_tftsd:SD TFT
label_read_tftsd_error:Erreur de lecture de la carte SD TFT !
label_tftsd_inserted:Carte insérée !
label_tftsd_removed:Carte retirée !
label_u_disk:Clé USB
label_read_u_disk_error:Erreur de lecture de la clé USB !
label_u_disk_inserted:Clé USB insérée !
label_u_disk_removed:Clé USB retirée !
label_onboardsd:SD interne
label_read_onboardsd_error:Erreur de lecture de la carte SD interne !
label_filament_sensor:Capteur de filament
label_filament_runout:Fin de Filament !
label_preheat:Préparer
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

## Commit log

2021-05-21 Updated parts for the Z reinforcement rod, add more clearance.
    [Back-corner-mirror.STL, Back-corner.STL, Z_renforcement-mirror.STL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]
2024-11-12 Update 3Dparts/STL
    [1.STEP, 1.stl, 2.STEP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]
